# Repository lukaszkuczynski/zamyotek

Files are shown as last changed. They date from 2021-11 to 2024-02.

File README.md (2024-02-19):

# TTbot (Track & Tell bot)
TTbot is a Jetson-powered object detection robot, linked with cloud AI systems and created in a decoupled manner. The idea of decoupling came from ROS that I haven't used as I wanted to have a purely Python solution.

## Demo
It moves, follows me and recognizes objects (somehow, we're still working to make it more reliable). Click the image below to see YT video...

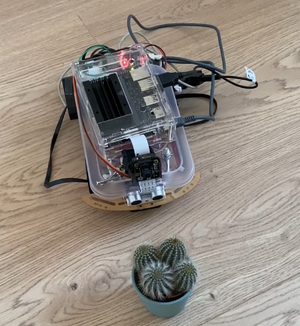
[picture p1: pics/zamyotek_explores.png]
IMAGE ALT TEXT (http://www.youtube.com/watch?v=LvrNewLIw1k "TTbot 1st photoshoot")


## Initial idea and change
The initial idea of the project was to follow objects and grab them with “arms” controlled by servo mechanisms. However, the custom trained Tensorflow detection algorithm based on SSD Mobilenet has rather low performance with small sized objects. Thus, the idea was altered, and now TTbot follows “big objects” (f.e. humans) and if presented with some object just ahead of him, he will speak what he sees.

## General idea
TTbot consists of *nodes* which are independently doing their job. They are publishing and subscribing to topics which are in the area of their responsibility. F.e. the node for sensor is sending distance measurements to `/sensor/distance` and *brain* node is listening to that and interpreting information to send commands to `/cmd/motor_move` where *motor* node is listening.
The main loop is reading data from the camera and sending coordinates of detected objects to a MQTT queue. Some of these nodes are displayed in the diagram below.

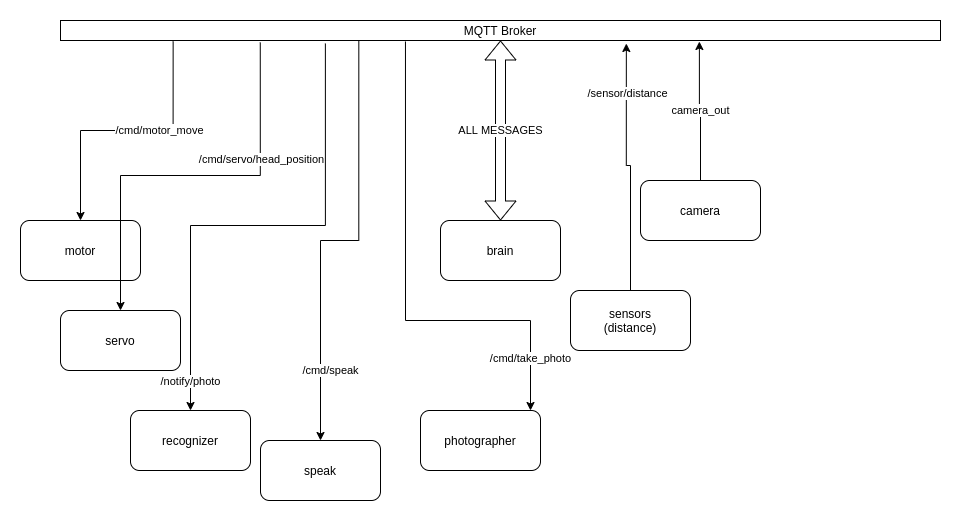
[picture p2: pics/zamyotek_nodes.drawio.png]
communication nodes


## Hardware
The main *brain* of the robot is Jetson Nano SBC. It runs Ubuntu on board so it is easily extendable and one can install needed Linux packages easily. It means I can run Python nodes too. Jetson Nano is capable of connecting electronics on 40 PIN header, [check out docs](https://developer.nvidia.com/embedded/learn/jetson-nano-2gb-devkit-user-guide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). You can also connect additional accessories to it via USB ports. Microcontrollers are OK to connect any sensors compatible to the Voltage level. And in case of problems I feel much more comfortable to burn the microcontroller than Jetson Nano.  Thus in this project there are several ESPs which are connected via USB cable and transmit data via it. They take both input voltage and data via the same USB cable.
Major parts used in the project are shown in the diagram, however the connections are not displayed. This is just to give the general overview of the project.

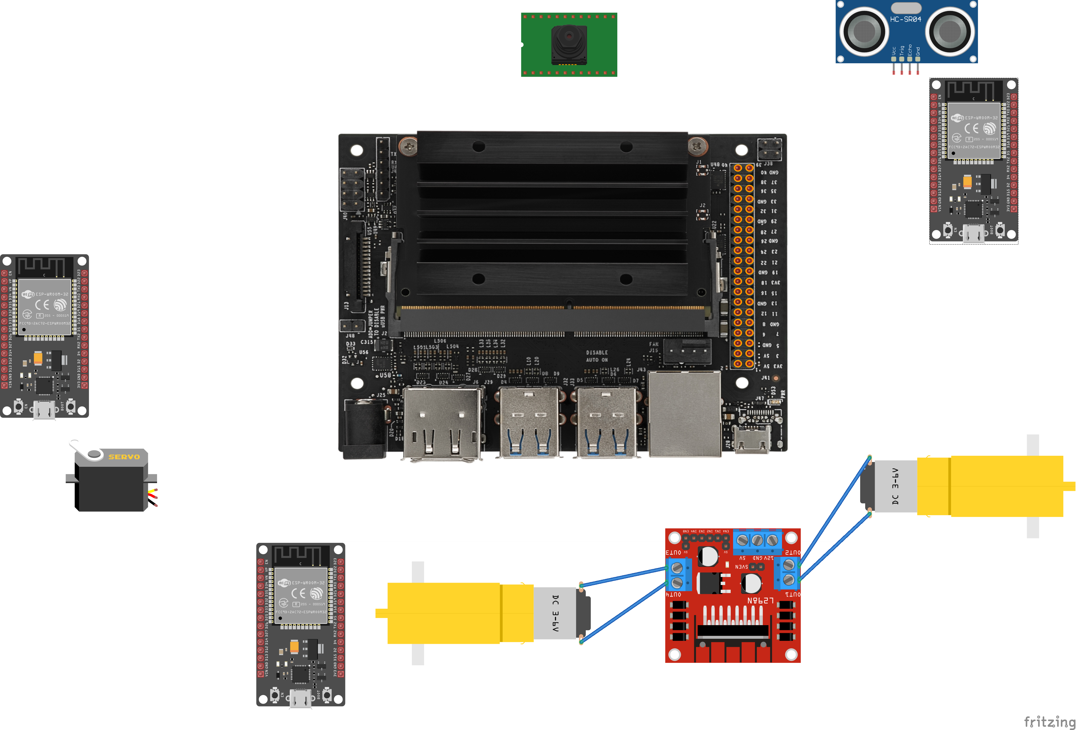
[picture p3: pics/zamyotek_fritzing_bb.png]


## Machine Learning
Jetson Nano comes with many pretrained models which work very efficiently. However the author of this project wanted to train his custom model. Unfortunately SSD Mobilenet v2 has pretty low performance on small objects. So the initial idea was changed as explained in the first sections and now the default algorithms as part of Jetson Pack are used. It gives pretty good performance when TensorRT in real time with 30 FPS. Image recognition of objects put just ahead of it are done with AWS and OpenAI.

## Cloud integration
To offload some ML calculations there were AWS services used to:
- recognize objects
- create speech fragments

Whenever an object is put in front of the robot, the photo is taken and according to the `TELLME` scenario it is sent to OpenAI service. Then the picture (so what TTbot sees) is interpreted with OpenAI Vision system. When the result is created it is put on speech synthesis topic. Speec synthesis is done with AWS Polly service.

## Brain modes
The main software element of the robot is working in the following modes:
 - `FOLLOW`
 - `TELLME`

In the `FOLLOW` mode TTbot is just the trying to detect and move in the direction of object classes. The `TELLME` scenario is executed when objects are detected by distance sensor.

In the `TELLME` scenario TTbot is trying to tell you what he sees. As for now Internet communication is required because it uses AI cloud services. In this scenario it moves camera down, takes a photo and sends to the recognition system. Then, if any “speaking node” is running it receives the command to play sound.

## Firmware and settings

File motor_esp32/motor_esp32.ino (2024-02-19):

#include <ESP32Servo.h>

const int leftB = 27;
const int leftF = 26; 
const int leftEnable = 25; 

const int rightB = 32;
const int rightF = 33; 
const int rightEnable = 13; 

//Servo leftServo;
int leftServoPin = 14;


// setting PWM properties
const int freq = 50;
const int leftMotor = 2;
const int rightMotor = 0;

const int servo = 4;

const int servoOpened = 5;
const int servoClosed = 30;



const int resolution = 8;

#define TURNING_TIME "250"
#define STOP_TIME 100      

#define DEFAULT_SPEED "120"
 
void setup(){
    // Allow allocation of all timers
  ESP32PWM::allocateTimer(0);
  ESP32PWM::allocateTimer(1);
  ESP32PWM::allocateTimer(2);
  ESP32PWM::allocateTimer(3);
  
  pinMode(leftF, OUTPUT);
  pinMode(leftB, OUTPUT);  
  pinMode(leftEnable, OUTPUT);  
 
  pinMode(rightF, OUTPUT);
  pinMode(rightB, OUTPUT);
  pinMode(rightEnable, OUTPUT);  
  
  // configure LED PWM functionalitites
  ledcSetup(leftMotor, freq, resolution);
  ledcSetup(rightMotor, freq, resolution);
  
  // attach the channel to the GPIO to be controlled
  ledcAttachPin(leftEnable, leftMotor);
  ledcAttachPin(rightEnable, rightMotor);

  ledcSetup(servo, freq, resolution);
  ledcAttachPin(leftServoPin, servo);
//  leftServo.setPeriodHertz(50);    // standard 50 hz servo
//  leftServo.attach(leftServoPin, 500, 2400); 
//
  ledcWrite(servo, servoOpened);
  Serial.begin(115200); 
}



void allStop() {
  digitalWrite(leftF, 0);
  digitalWrite(leftB, 0);
  digitalWrite(rightF, 0);
  digitalWrite(rightB, 0);
}

void loop(){
  if(Serial.available()){
    String full_command = Serial.readStringUntil('\n');
    int i1 = full_command.indexOf(',');
    int i2 = full_command.indexOf(',', i1+1);
    String cmd_arg = DEFAULT_SPEED;
    String cmd_arg2 = TURNING_TIME;
    String command = full_command;
    if (i1 > 0) {
      command= full_command.substring(0, i1);
      if (i2 > 0) {
        cmd_arg = full_command.substring(i1+1, i2);
        cmd_arg2 =  full_command.substring(i2+1);

      } else {
        cmd_arg = full_command.substring(i1+1);
      }
    }
    int turningSpeed = cmd_arg.toInt();
    int turningTime = cmd_arg2.toInt();

    Serial.printf("Command received %s, arg1=%s, arg2=%s \n", command, cmd_arg, cmd_arg2);
    if (command.equals("left")) {
      allStop();
      digitalWrite(leftB, HIGH);
      digitalWrite(rightF, HIGH);
      ledcWrite(leftMotor, turningSpeed);
      ledcWrite(rightMotor, turningSpeed);
      delay(turningTime);
      allStop();
      delay(STOP_TIME);
    } else if (command.equals("right")) {
      allStop();
      digitalWrite(leftF, HIGH);
      digitalWrite(rightB, HIGH);
      ledcWrite(leftMotor, turningSpeed);
      ledcWrite(rightMotor, turningSpeed);
      delay(turningTime);
      allStop();
      delay(STOP_TIME);
    } else if (command.equals("stop")) {
      allStop();
    } else if (command.equals("ahead")) {
      allStop();
      digitalWrite(leftF, HIGH);
      digitalWrite(rightF, HIGH);
      ledcWrite(leftMotor, turningSpeed);
      ledcWrite(rightMotor, turningSpeed);
    } else if (command.equals("open_gate")) {
      ledcWrite(servo, servoOpened);
    } else if (command.equals("close_gate")) {
      ledcWrite(servo, servoClosed);
//       leftServo.write(leftServoClosed);
    }
  }


}

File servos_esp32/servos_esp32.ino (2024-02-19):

#include <ESP32Servo.h>
#include <Adafruit_NeoPixel.h>

int leftServoPin = 4;
int rightServoPin = 26;

const int NEOPIXEL_PIN = 23;
const int NEOPIXEL_LED_COUNT = 8;

const int freq = 50;
const int resolution = 8;

const int leftServoOpened = 110;
const int leftServoClosed = 30;


const String DEFAULT_DEGREE = "0";

const int steps = 10;
const int stepDelay = 50;

Servo leftServo;
Servo rightServo;

Adafruit_NeoPixel pixels = Adafruit_NeoPixel(NEOPIXEL_LED_COUNT, NEOPIXEL_PIN, NEO_GRB + NEO_KHZ800);
 
void setup(){
  leftServo.setPeriodHertz(50);    // standard 50 hz servo
  leftServo.attach(leftServoPin, 500, 2400); 
  rightServo.setPeriodHertz(50);    // standard 50 hz servo
  rightServo.attach(rightServoPin, 500, 2400); 
  Serial.begin(115200);
  pixels.begin();
  closeGate();
}

void openGate() {
  int step_size = abs(leftServoClosed - leftServoOpened) / steps;
  for (int pos=leftServoClosed; pos<leftServoOpened; pos+=step_size) {
    leftServo.write(pos);  
    delay(stepDelay);
  }
}

void closeGate() {
  int step_size = abs(leftServoClosed - leftServoOpened) / steps;
  for (int pos=leftServoOpened; pos>leftServoClosed; pos-=step_size) {
    leftServo.write(pos);  
    delay(stepDelay);
  }
  
  leftServo.write(leftServoClosed);
//  rightServo.write(rightServoClosed);  
}

void setColor(String color) {
  Serial.printf("Setting color to %s\n", color);
  int r = 0;
  int g = 0;
  int b = 0;
  if (color == "green") {
    g = 255;  
  } else if (color == "red") {
    r = 255;
  } else if (color == "orange") {
    r = 255;
    g = 165;
  } else if (color == "white") {
    r = 255;
    g = 255;
    b = 255;
  } else if (color == "blue") {
    r = 50;
    g = 100;
    b = 255;
  } else {
    // black is fallback
  }
  for (int k = 0; k < NEOPIXEL_LED_COUNT; k++) {
    pixels.setPixelColor(k, pixels.Color(r, g, b));
  }
  pixels.show();
}

void loop(){
  if(Serial.available()){
    String full_command = Serial.readStringUntil('\n');
    int i1 = full_command.indexOf(',');
    int i2 = full_command.indexOf(',', i1+1);
    String cmd_arg = DEFAULT_DEGREE;
    String command = full_command;
    if (i1 > 0) {
      command= full_command.substring(0, i1);
      cmd_arg = full_command.substring(i1+1);
    }
    int servoDegree = cmd_arg.toInt();
    Serial.printf("Command received %s \n", command);
    if (command.equals("open_gate") || command.equals("godown")) {
      openGate();
      Serial.println("godown finished");
    } else if ((command.equals("close_gate") || command.equals("goup"))) {
      closeGate();
      Serial.println("goup finished");
    }
    if (command.equals("setColor")) {
      setColor(cmd_arg);
    }
  }
}

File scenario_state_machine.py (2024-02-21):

"""This defines module for a State Machine for TTbot"""

# pylint: disable=missing-function-docstring, missing-class-docstring, broad-exception-raised
import logging
import os
from datetime import datetime, timedelta
from enum import Enum
from time import sleep


def setup_logger(name, log_folder="logs"):
    log_filename = os.path.join(log_folder, name + ".log")
    logger = logging.getLogger(name)
    logger.setLevel(logging.DEBUG)
    # create file handler which logs even debug messages
    fh = logging.FileHandler(log_filename)
    fh.setLevel(logging.DEBUG)
    # create console handler with a higher log level
    ch = logging.StreamHandler()
    ch.setLevel(logging.DEBUG)
    # create formatter and add it to the handlers
    formatter = logging.Formatter(
        "%(asctime)s - %(name)s - %(levelname)s - %(message)s"
    )
    ch.setFormatter(formatter)
    fh.setFormatter(formatter)
    # add the handlers to logger
    logger.addHandler(ch)
    logger.addHandler(fh)
    return logger


class ScenarioResult(Enum):
    NEXT_STEP = 1
    TIMEOUT = 2
    FINISHED = 0
    INACTIVE = 3
    ILLEGAL_STATE = 4
    FAILED = 5


class StepFactory:
    def step_from_config(self, cfg, logger, mqtt_node):
        if cfg["type"].lower() == "sleep":
            return SleepStep(cfg, logger)
        elif cfg["type"].lower() == "send_mqtt":
            return MqttSendStep(cfg, logger, mqtt_node)
        elif cfg["type"].lower() == "receive_msg":
            return ReceiveMsgStep(cfg, logger)


step_factory = StepFactory()


class ScenarioStateMachine:
    def __init__(self, name, steps, mqtt_node=None, min_interval=timedelta(seconds=0)):
        self.logger = setup_logger(name)
        self.name = name
        if len(steps) < 1:
            raise Exception("Cannot initiate state machine with 0 steps")
        self.logger.info("Creating scenario '%s' with %d steps", name, len(steps))
        self.steps = [
            step_factory.step_from_config(step, self.logger, mqtt_node)
            for step in steps
            if isinstance(step, dict)
        ]
        # self.logger.debug(steps)
        self.current_step_no = -1
        self.active = True
        self.storage = {}
        self.last_run = datetime.strptime("2000-01-01", "%Y-%m-%d")
        self.min_interval = min_interval

    def can_run(self):
        from_last_time_interval = datetime.now() - self.last_run
        return from_last_time_interval > self.min_interval

    def start(self):
        if not self.can_run():
            self.logger.warning(
                "I will not run scenario %s again,because it was just run recently",
                self.name,
            )
            return ScenarioResult.ILLEGAL_STATE
        self.active = True
        self.current_step_no = -1
        self.__execute_next_step(msg=None)

    def __execute_next_step(self, msg=None):
        self.current_step_no += 1
        step = self.__current_step()
        if step is None:
            self.finish_scenario()
            # self.current_step_no -= 1
            return ScenarioResult.FINISHED
        self.logger.info("Executing step#%d: %s", self.current_step_no, step.name)
        step.execute(msg, self.storage)
        if not step.is_async:
            return self.__execute_next_step(msg)
        return ScenarioResult.NEXT_STEP

    def __current_step(self):
        if self.current_step_no >= len(self.steps):
            return None
        return self.steps[self.current_step_no]

    def __save_to_storage_if_needed(self, step, msg):
        keyname = step.save_to_storage_key
        if keyname:
            self.storage[keyname] = msg

    def process_message(self, msg):
        # self.logger.debug("Processing message")
        # self.logger.debug(msg)
        if not self.active:
            return ScenarioResult.INACTIVE
        if self.__current_step().is_timeout():
            self.logger.warning("Detected timeout.. Will finish the scenario")
            self.finish_scenario()
            return ScenarioResult.TIMEOUT
        if self.__current_step().is_waiting_for(msg):
            self.logger.debug("I was waiting for you, msg %s", msg)
            if msg["msg"].startswith("error"):
                self.logger.warning(
                    "error detected, I will not proceed to the next step %s", msg["msg"]
                )
            else:
                self.__save_to_storage_if_needed(self.__current_step(), msg)
                return self.__execute_next_step(msg)
        else:
            return None

    def interrupted(self):
        self.logger.info("checking interrupt %d", self.current_step_no)
        return not self.active and (self.current_step_no < len(self.steps))

    def __run_finally_steps(self):
        for n in range(self.current_step_no, len(self.steps)):
            step = self.steps[n]
            if step.is_finally_step():
                self.logger.info("Executing one of finally steps:")
                step.execute()

    def finish_scenario(self):
        self.logger.info("Scenario finished!")
        self.__run_finally_steps()
        self.last_run = datetime.now()
        self.active = False


class Step:
    def __init__(self, cfg, logger) -> None:
        self.name = cfg["name"]
        self.logger = logger
        if not "timeout" in cfg:
            self.timeout = 0
        else:
            self.timeout = cfg["timeout"]
        self.save_to_storage_key = cfg.get("save_to_storage_key", None)
        self.read_from_storage_key = cfg.get("read_from_storage_key", None)
        self.is_finally = cfg.get("is_finally", False)
        self.was_run = False
        self.started = None

    def is_waiting_for(self, msg):
        return False

    def is_timeout(self):
        now = datetime.now()
        if (now - self.started).total_seconds() > self.timeout:
            return True
        return False

    def execute(self, msg=None, storage=None):
        self.started = datetime.now()
        self.was_run = True

    def is_finally_step(self):
        return self.is_finally


class SleepStep(Step):
    def __init__(self, cfg, logger):
        super().__init__(cfg, logger)
        self.is_async = False
        self.waiting_time = cfg["waiting_time"]

    def execute(self, msg=None, storage=None):
        super().execute(msg, storage)
        self.logger.debug("Step name %s", self.name)
        self.logger.info("Executing sleep for %s seconds.", self.waiting_time)
        sleep(self.waiting_time)
        self.logger.debug("Waiting finished")
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

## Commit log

2021-10-15 Simple motor driver for RPi
2021-10-15 Fritzing added
    [fritzing.fzz]
2021-10-22 Default camera of Jetson
2021-10-22 Camera sends center details
2021-10-22 ready to move motors
2021-10-22 Fritzing export
    [fritzing.fzz]
2021-10-22 ESP32 PWM controller for motors
2021-10-23 Motor controller, brain improved
2021-10-30 Can open and close gates using servo
2021-10-31 New ESP enters the stage 'cause we bought USB hub
2021-10-31 Can fetch data from sensors and push it to MQTT topics
2021-11-06 Motor program done aright, PWM on ENable pins, not directional ones from LM298N
2021-11-09 turn off buggy servo, speed can be provided with params
    [motor_esp32.ino, sensors_esp32.ino]
2021-11-16 Separate ESP to control servos
2021-11-16 Servo separate node
2021-11-17 Camera config in yaml, reloadable
2021-12-11 Rekognition node listens to camera.
2021-12-12 One servo now, only to serve as a camera head
2021-12-26 camera image sent to detection before overlay
    [fritzing.fzz]
2021-12-27 README done
    [fritzing.fzz]
2024-02-05 new Jetson system
